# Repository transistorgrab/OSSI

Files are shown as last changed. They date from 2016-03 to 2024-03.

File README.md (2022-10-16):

# OSSI
Open Source Solar Inverter - Software, Hardware, Mechanics

This repository initially clones all content from the former Sourceforge hosted project site (https://sourceforge.net/projects/os-si/). Since the outages on Sourceforge became more frequent, I decided to change over to Github which seems more reliable at this time.

This project aims to build an Open Source (Software and Hardware) Solar Inverter.

The goal is to design a solar inverter with parts that are available trough common distributors with no special manufactured parts.

All documentation (software, hardware, mechanics) is open and free to use by everyone.

Solar inverters can be very complex devices to build and there is a lot to learn on the way.

Join, collaborate, learn and help make the world a better place.

The sun shines for everyone! 😊

The current activities take place in the [Wiki](https://github.com/transistorgrab/OSSI/wiki), where we collect the requirements.

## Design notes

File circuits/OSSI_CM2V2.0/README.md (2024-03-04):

# O.S.S.I Control Module 2 V2.0

This version of the control module contains various improvements over version 1.0/1.1 of the module.

## Breaking Changes
### Different controller pin mapping.
This change was necessary due to an oversight when assigning pins to PWMs. Now the bridge controlling PWMs are assigned to timer 1 channel 1 and 1N and channels 2 and 2N which now implements requirement SOFT-3002.

However, the module footprint still shows the same pin mapping as before.

## Improvements
The board now features an I²C EEPROM for storage of parameters, settings, counters and other data that should be protected between firmware updates. This is an actual EEPROM and not a Flash due to vastly better data retention and write cycles.

The package of the 8 pin ICs on the module are now changed to TSSOP to improve use of board space.

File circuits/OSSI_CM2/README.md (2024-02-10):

This is the Control Module 2.

It's based on a STM32L412 ARM M4 microcontroller.

It's designed for 3.3 V input voltage.

It features a 2.5 V and 1.25 V reference voltage source and a digital temperature measurement IC.

On it's pins provides:
* 3.3 V filtered analog voltage
* 2.5 V reference voltage, 1.5% accuracy
* 1.25 V reference voltage, 1.5% accuracy
* 8 analog inputs
* 11 digital outputs
* 1× UART (RX/TX)
* 1× I²C (Clk/Dat)

[O.S.S.I. CM2 pinout](./bom/OSSI_CM2-Pinout.pdf "Pinout of the O.S.S.I. Control Module 2")

## Remarks
When building the board by hand the voltage devider R132/R133 can be realized by using 1% resistors. However, one needs to value-match them to be within the 0.1% tolerance.

For example: When using 1 kΩ resistors they need to be within 1 Ω difference to each other.

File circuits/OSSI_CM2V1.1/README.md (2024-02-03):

# O.S.S.I Control Module 2 V1.1

This version of the control module contains only bug fixes to version V1.0.

These are either changes to the BOM (values of components) or changes on the PCB which are only fixable on version 1.0 by hardware modifications.
Changes to the PCB are limited to fixes that restore the original design idea. E.g. connection of a voltage divider to the correct net to remove undesired voltage drop.
Component references and positions are kept the same as on version 1.0.

If there are hardware modifications that add components, add functionality or remove functionality these must be done in a version 2.0 of the module.

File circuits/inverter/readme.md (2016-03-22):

This directory contains all schematics for the inverter.
It is planned to place all components on a single board (electronics and power electronics) since this is the best way to keep the costs down and keep the system complexity low.
Mulitple boards require connectors and cables. Connectors can go bad over time (corroding contacts due to moisture), cables add their own problems due to EMI and ground bounce. The connection between cable and connector is an additional source for failure.

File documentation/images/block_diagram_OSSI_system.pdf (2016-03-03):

Author: | os-si-man | Date: | 2015-03-22

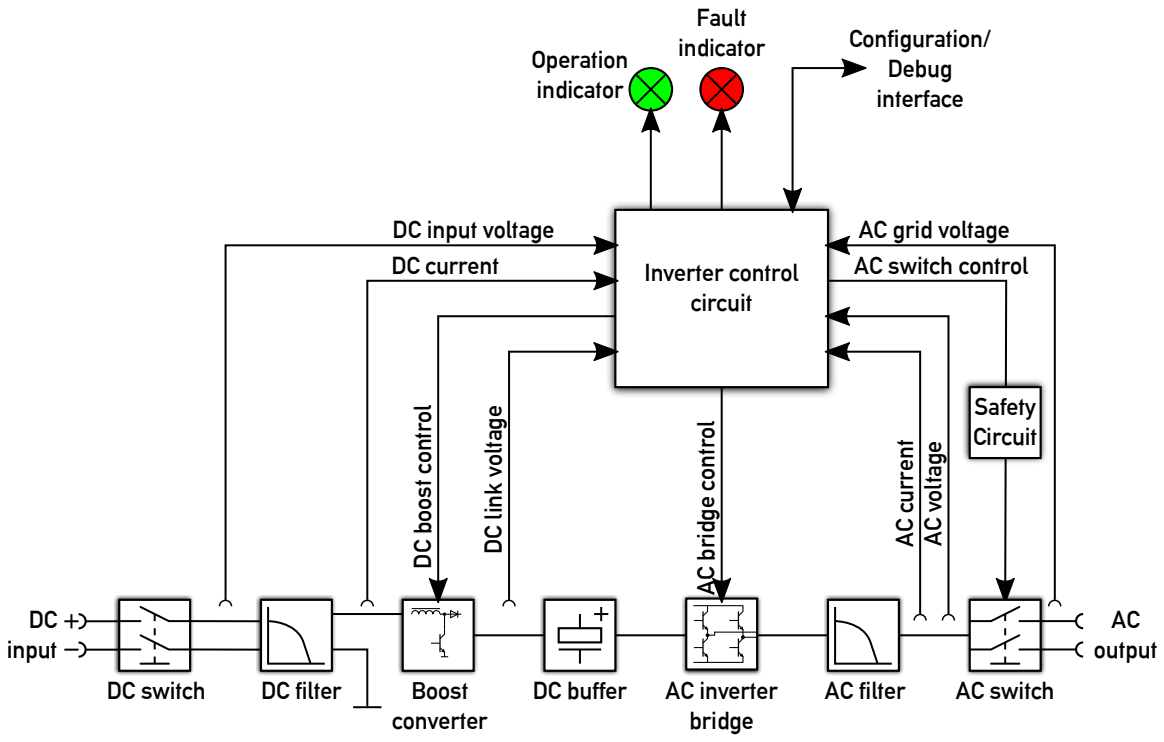
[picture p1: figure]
DC input; DC switch; DC filter; Boost; converter; AC output; AC switch; DC boost control; AC bridge control; AC current; AC voltage; AC switch control; Operation indicator; Configuration/ Debug interface; Fault indicator; DC input voltage DC currentDC link voltage; Inverter control circuit; AC grid voltage; Safety Circuit; AC inverter; AC filter; bridge; DC buffer

Project: | Open Source Solar Inverter (OSSI)

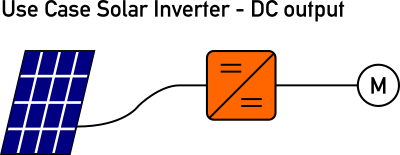
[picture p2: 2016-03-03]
documentation/images/OSSI_use_case_solar_dc.png

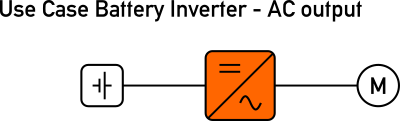
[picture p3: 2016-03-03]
documentation/images/OSSI_use_case_battery_ac.png

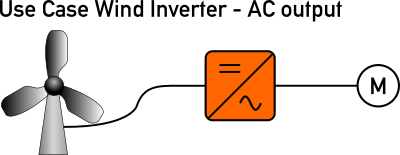
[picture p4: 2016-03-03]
documentation/images/OSSI_use_case_wind_ac.png

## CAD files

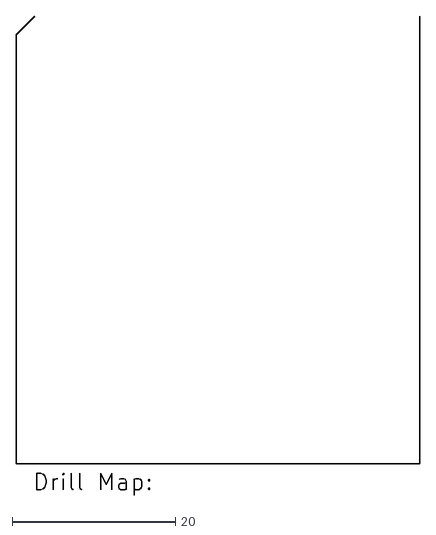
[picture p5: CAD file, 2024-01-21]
circuits/OSSI_CM1/fabrication/OSSI_CM1-NPTH-drl_map.dxf
49.5 x 58.7

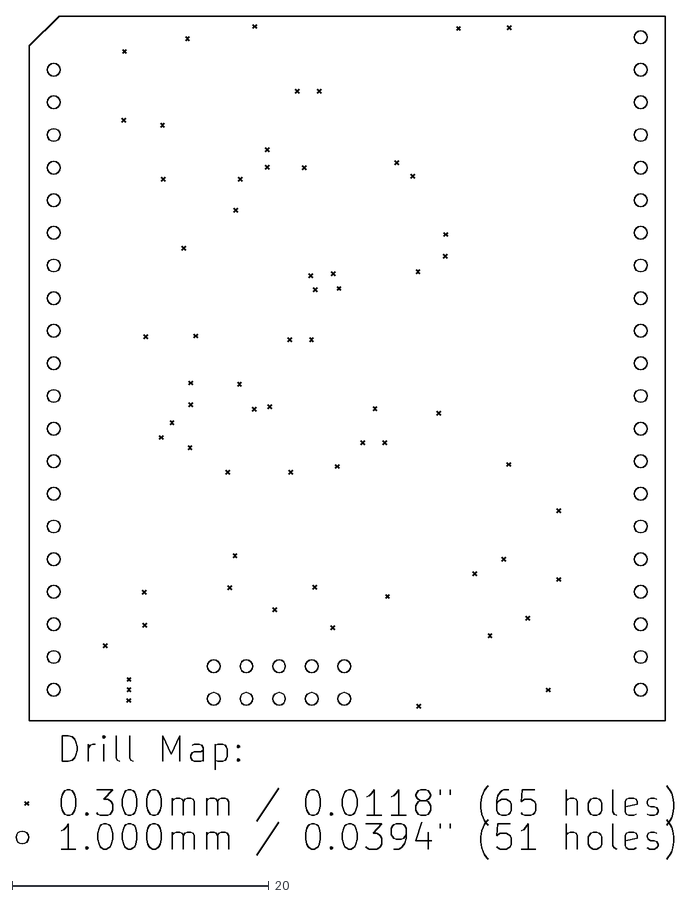
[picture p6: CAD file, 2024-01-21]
circuits/OSSI_CM1/fabrication/OSSI_CM1-PTH-drl_map.dxf
51.2 x 65.6

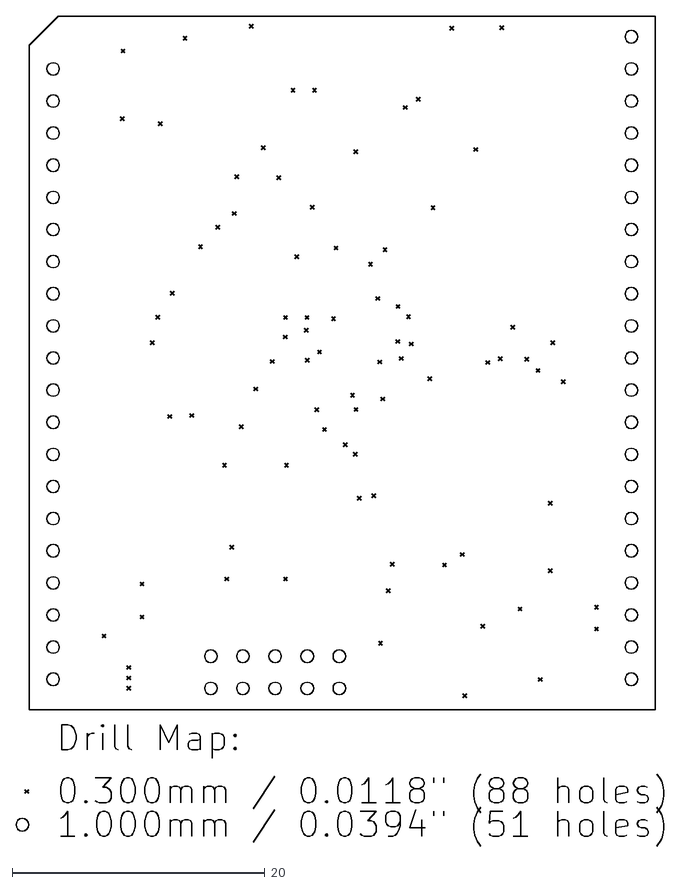
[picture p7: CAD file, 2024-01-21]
circuits/OSSI_CM2/fabrication/OSSI_CM2-PTH-drl_map.dxf
51.2 x 65.6

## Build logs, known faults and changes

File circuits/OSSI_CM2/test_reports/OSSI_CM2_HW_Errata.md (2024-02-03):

# Errata for Board Revision V1.0 of Control Module 2

## Error
The voltage divider for reference voltage ```1V25_REF``` is connected on the wrong signal (```2V50_REF```). This leads to a too low reference voltage output on the signal ```1V25_REF```. 

## Solution
The voltage divider ```R133```–```R132``` needs to be connected directly to ```pin 7``` of ```U104```.
To achieve this one needs to cut the signal trace for ```2V50_REF``` between ```R134``` and ```R133``` and the trace between  ```R133``` and ```pin 3``` on connector ```X201```.
Then solder a wire from ```R134``` to ```pin 3``` on connector ```X201``` and a wire from the signal connecting ```pin 7``` of ```U104``` and ```R134``` to the now unconnected pad of ```R133```.

This error is **solved on Board Revision V1.1**.

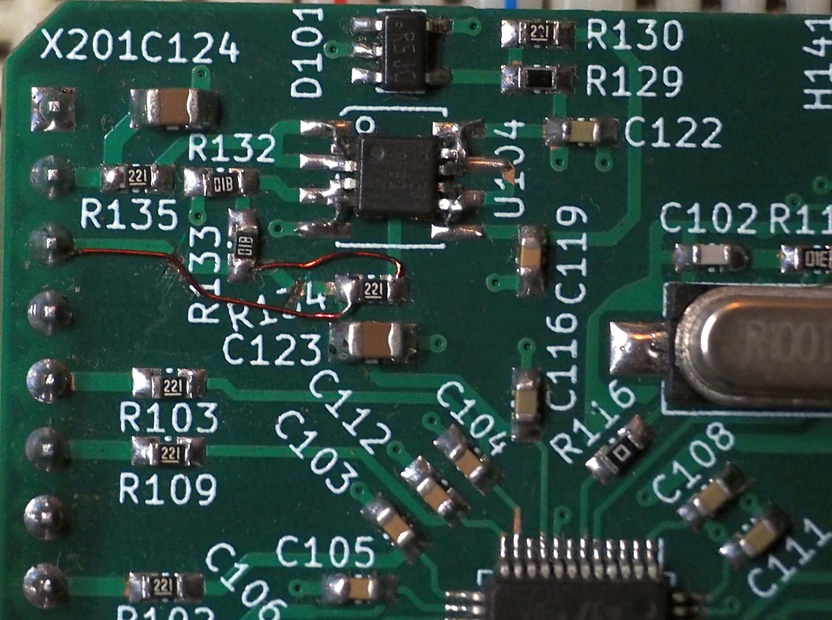
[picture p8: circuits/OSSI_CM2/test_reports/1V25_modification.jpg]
1V25 modification 1V25_REF modification on CM2 V1.0


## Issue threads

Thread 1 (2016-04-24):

Need anything?

tyrel, 2016-04-24:
Hi! I ran across your project because I was looking to see if there was anyone working on an open-source solar inverter, in order to get around problems I and my friends have experienced with trying to get data from our proprietary inverters. So I'm excited to see that you're working on this. I would love to help.

I have some limited knowledge of electronics (e.g. I know what a resister does and why they are used, but don't know how to figure out which one to use), enough to put together a weather station from scratch. I know how electricity works at the atomic level. But I'm primarily a software guy, and have done projects on Raspberry Pi and Arduino, and other low-level stuff like operating systems development. I'm currently working on a remote solar-powered weather station using a Raspberry Pi with ZigBee communications.

As far as solar: I have a 12 kW solar array, my wife works at a solar installer, and I know people at a local solar module manufacturer. I know how it works, I know what MPPT is, etc.

I've looked a bit at your wiki but have more to go through. Is there somewhere, based on my skills, you can recommend that I start looking at? Any questions I can help find answers to?

Thanks!

transistorgrab, 2016-04-24:
Hi Tyrel,

Thanks for your message.
I'm currently stuck at the power electronics stuff like which inductor to choose our how to realize the power inverter circuit since my background is the electronics and analog part.
However, I also would love to get support on the software side of things.
I'm proposing using a RTOS as a base like FreeRTOS (http://www.freertos.org).
But this needs to be ported and set up for the chosen controller. Also a basic structure for the scheduling of all the required tasks needs to be defined and so on. The software/firmware is a project of itself… ;)
So whatever you want to do on this side of the project (and planning) is greatly appreciated.
I keep all the documentation in the Wiki because I find it the easiest way with no tool required.

Best regards,
  André

stardust85, 2021-11-21:
Hi, I can offer my limited very knowledge of hw programming (from high and a bit from university) and tons of experience of sw development experience...

I am also a proud owner of a 4.56 kWp hybrid roof-top sytem based on the RCT inverter, BMS and batteries.

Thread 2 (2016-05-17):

Expansion to battery use

sheppy99, 2016-05-17:
Is it worth expanding your project at some stage to include use with batteries? I'm thinking some sort of monitored situation whereby assuming the battery has sufficient charge, and assuming there is import electricity, that the inverter supplies just enough output if headroom is available to reduce the import to  a few watts. It could use a feed from Open Energy Monitor or similar to provide the instantaneous import / export power information.
In many parts of the world exported energy is something to be avoided, and importing is expensive

transistorgrab, 2016-05-18:
Yes. There is no principal obstacle to use batteries as an input source.
It's one of the use cases. You only need to adjust the input voltage range to not drain the battery too low and also you have to disable the "Maximum Power Point" algorithm. This is "only" a software issue. Nothing that the hardware does not support.
For communication a UART (serial) port is provided in the design, usable for debug or other uses.

sheppy99, 2016-05-18:
Thanks for the reply, will it be possible to vary the output of the inverter so generated power matches used power? I guess several could be built as a lower power design and switched as needed but that seems a little inelegant

transistorgrab, 2016-05-20:
The first can also be achieved via communication and setting a current limit. But this would require an external device that monitors energy flow from and to the grid. I think most of the energy flow control intelligence then needs to be placed in that device, since I fear that would exceed the computing power of the main controller.
The second could be achieved in the software that keeps track of the state of charge of the battery. but it depends on what kind of Lithium battery is in use. You need definitely a battery pack with a battery management system (BMS). (The inverter can not track all cells of a battery pack.)
The BMS (at least those I know) keep track of the state of charge of the battery. It remains to implement a communication interface to the battery/BMS. Some use CAN, I think there are also some that use other serial interfaces.
My opinion is, that lithium batteries are quite complicated in handling and operation. Therefore at least in the first iteration of the inverter only lead batteries can be used (no additional communication required, only cut off voltage must be respected).

sheppy99, 2016-05-22:
I wonder if the inverter could take something like a MQTT message to tell it how much power to output? That could be generated by an energy monitoring system such as Open Energy Monitor, with an automation system such as Openhab stacked on top. If the inverter sent out its status, decisions could be made on both power demand and charge remaining and the requested power output could be modified in light of reported input voltage.
The automation system can take control of what the inverter is asked to do, with the inverter maybe going into a failsafe mode if it hasn't received a valid message for a period of time.
Obviously a BMS is very important for both safety and longevity!

transistorgrab, 2016-06-08:
Seems possible, just depends on how much overhead the communication protocol generates. It may be necessary to have a gateway that translates "inverter protocol" to "(home) automation protocol".
On the other hand if there is a light weight protocol freely available that could be implemented as the standare protocol for the inverter communication.
For example Modbus could be used ([freemodbus.org](http://www.freemodbus.org/)) but I don't know about the specifics.

Closed 2019-08-01.

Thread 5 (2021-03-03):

i would like to help

Thorbijoern, 2021-03-03:
Hi,

i'm researching inverter design for some time now, because i noticed a lack of open source inverter projects. There are open source MPPT charge controllers and BMS, but no inverters. I only recently found this project but think your work is great!
I have documented a lot of stuff i found about inverters here: https://thorbijoern.github.io/wiki/#inverter%20(Wechselrichter) maybe it is helpful to you (i need to do some ordering though).
I would like to contribute to this project, because the goal of my researching was to create my own design, but i still have a lot to learn.

i've only read a small part of the documentation as of yet, but in #1 you said you would need help on the software side (even though it's from 2016). I'm a software developer by profession and could help you with that part.
I also could improve the documentation a bit.
My electronics knowledge is limited and i haven't done anything powerelectronics myself yet, but i think i have a good overview.

this project also intersects with the projects from https://libre.solar/ and https://www.ose-germany.de/ (https://wiki.opensourceecology.de/Open_Source_Ecology_Germany) and others and compatibiltity/interoperability between the designs would be great.

Tank you for the great work so far!

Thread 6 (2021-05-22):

Project status

pixelpoppul, 2021-05-22:
Is this project still continued or forgotten?

transistorgrab, 2021-05-25:
Hi, it's not forgotten but dormant.

I have other things currently taking up my time. But if you're interested in helping I would gladly support and wake it up again and switch my priorities. :) It's a bit boring to do all the things alone…

pixelpoppul, 2021-05-25:
Would be great to continue given there arent much open source systems on the internet and the solar market is kinda booming :) mention when you left off and we can continue it

transistorgrab, 2021-05-25:
Take a look at the latest Kicad files (just uploaded my latest modifications). I think I have a lot of the electronics in a good state. However, power electronics like AC inverter bridge and drivers are still open. This is the part where I have not the deepest knowledge and need to learn most. Which is why it's the last to be finished.

Software is totally open. I figured it's not much use to start anything software as long as it's not defined what hardware will be there and what needs to be considered in software.

Also look into the wiki section here. I documented as much as possible there. Read it over and see if it helps to understand what I wanted to create here. I'm open to feedback so don't hold back.

pixelpoppul, 2021-05-25:
Its not THAT complicated as three basic things
Sensing
Driving the hbridge
Output control

I have rough schematics to do all three along with the hbridge  ill look at the kicads once i get time   like 20mins from now

pixelpoppul, 2021-05-26:
do you have a email i could send you a sample file to? it has almost all of the things required(almost) all already kinda made

transistorgrab, 2021-05-26:
you can send me your file to ansc _dot_ de _at_ gmail _dot_ com

looking forward to it :)

pixelpoppul, 2021-05-29:
I think i missed the page we were on  the file i sent was for a microinverter as this project looks like a string inverter.  I think it will be easier on you to build a microinverter as its easy to code and design and is also cost efficient  :)

Thorbijoern, 2021-06-01:
i'm happy to see that there is some new developments here, after i didn't receive an answer on #5 i worried this is dead.

i think the types of inverters (string, micro, etc.) are a bit confusing.
Judging from OSSI-2002 from [Requirements Page](https://github.com/transistorgrab/OSSI/wiki/The-Requirements) it seems like a micro inverter ist the goal, but it should also have a very high input voltage like string inverters OSSI-2003.
I  don't know how one can accieve input ranges from ~18V for single solar panels and ~12V or ~24V for batteries, up to 600V. But i also don't know how one designs such boost stages and https://github.com/transistorgrab/OSSI/wiki/Electronics-and-Electrical#power-supply also talks about problems with the input range and efficiency.

libre.solar is also cool, they have some open MPPT charge controller designs and they make documentation on the design princibles, controlling and other things which might be helpful here too.

pixelpoppul, 2021-06-01:
There are solar panels tjat output 24v and custom ones do as much as 50!.
Boost stages are nothing but just the transformer stepping the sine wave made by the full h bridge system. Bssic but works
SPWM gives a higher return range and increases efficiency but it is hsrd to code on a microcontroller as the timings need to ne near perfect for a grid level pure sine wave inverter.

transistorgrab, 2021-06-02:
@Thorbijoern Sorry for missing your message on #5. With the current situation it's a bit stressful to keep everything monitored.

There are different design goals here because I want to be able to realize different devices with as few as possible changes to the overall design. It's not aimed towards making the cheapest inverter on the planet but as a learning experience. I hope to make a as good as possible documentation about all design decisions for others to see what it takes to make a working inverter.

String inverters have multiple panels in series. Microinverters connect to one or two panels in parallel.
I think it is possible to have a small solution that only takes one panel and charges a 12 V battery. But also a solution that takes a panel string and charges a higher voltage battery.
Or it runs off a battery instead of a solar panel.

It's great that there are so many different projects now. :)

Just take a look at what is already there and ask questions or propose some measures or changes. I still have hopes that some day there will be a prototype. :D

casainho, 2022-02-16:
Hi.
I would be interest in having a Telegram channel so the development could be discussed. I am on 2 channels doing real development for EBike and EScooter motor controllers, all OpenSource projects.

@transistorgrab would you like to created a Telegram channel for developers on this project?

Congratulations on this project, Solar and Battery seems will be a BIG thing in next years!!

transistorgrab, 2022-10-03:
Hi @Saphira8105,
This project is dormant at the moment. Due to real life happening I did not find much time for it.
However, if someone joins I would gladly revive it.
Main problem at the moment is the power electronics stuff. I'm not an expert at this and this is a blocker for the actual important part of "inverter".
Some side-projects showed me that one may think it's OK but when actually operating the thing it can show unexpected behaviour and break if you do not know exacly what you are doing.

transistorgrab, 2022-10-05:
This project is still open for development. However, I'm stuck at the power electronics part, where the actual "inverter" function is affected. I'm no expert on this and had some experiments done that showed if you don't know what you're doing it will not work (reliably). So if you know someone who has some experience with power electronics, that could give the project new life.

pixelpoppul, 2022-10-05:
I'll surely take a look at it but can you brief what's not working reliably? Is the bridge not timed right or what is it?On Oct 5, 2022 9:37 PM, "André S." ***@***.***> wrote:
This project is still open for development. However, I'm stuck at the power electronics part, where the actual "inverter" function is affected. I'm no expert on this and had some experiments done that showed if you don't know what you're doing it will not work (reliably). So if you know someone who has some experience with power electronics, that could give the project new life.

—Reply to this email directly, view it on GitHub, or unsubscribe.You are receiving this because you authored the thread.Message ID: ***@***.***>

transistorgrab, 2022-10-05:
Currently there is still no actual hardware. The schematics shows the latest version.
To summarize: on the DC input there still needs to be decided what is the right IGBT for the boost converter. There is only a generic part in the schematics.
The inverter bridge is completely blank. There is input required what are the right components for the desired power class.
For the Bridge drivers there is a first suggestion but the circuit is not designed. But this is just a minor issue.

Adding to that the component selection needs to be documented in a way that makes it clear without doubt why a certain component or ciruit was chosen to make it easier for later contributors if a change is required.
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
pixelpoppul, 2022-10-05:
Looks like we have a solid plan, let's just hope we don't get the magic smoke XD. 600w is doable and the spwm may need some tuning because sine waves made by the inverter will be absolutely distorted due to the loads

HyGy, 2022-10-11:
Is there now a board/parts list to build?

It will be good if this thing is supported by ESPHome, and then we can integrate it for example to homeassistant.

I think what is required:
- battery charging (Settable parameters)
- solar input
- if there is not enough power in the batteries/solar then add suplement from the grid
- serial output/input to control/monitor the device parameters/consumption/voltages

What is a really usable a 5KV system I think. Bot for start about 700VA is good.

What is the state now?

transistorgrab, 2022-10-16:
Hi @HyGy,

There is still no fixed parts list. Some parts of the circuit are still not finally designed yet.
Additional problem that came up in the last few days when I reviewed the design is that the chosen microcontroller is currently not available anywhere.
If anyone has an idea what a good and available second source is, I'm open for suggestions.
I found some AVR32 based parts, PIC32 based parts even a Renesas part on digikey but I cannot say how feasable they are for this application.

Regarding ESPHome I don't think this should be intergrated into the controller software. I'm more thinking about an open protocoll where an external interface-converter then implements the required protocoll for home automation. e.g. an ESP32 that talks on one end to the inverter (via wired interface) and provides the desired protocoll via WiFi.
This would also solve the problem of isolation of the communication interface because the ESP32 could be connected to the hot potential of the inverter.

Waynedejager1, 2022-11-08:
I have a vested interest in this space and would like to help where possible. My main area of interest would be in the 100KW range of product and would be wiling to assist with the project. Areas where i can offer assistance :- 1) Current commercial unit damaged samples 2) Development funding once the core dev team is established 3) Procuring samples and testing in real life application.

If this appeals to you Andre @transistorgrab then please keep me informed. Wayne

transistorgrab, 2022-11-09:
Hi @Waynedejager1,

thanks for your offer.

Currently I'm back on square 1 regarding the main controller of the device.

The one I picked when starting the project looked like the perfect candidate.
However, currently it's nowhere available and I'm not a big expert on controllers to know which of the currently available parts would fit the bill. Also prices for components available now seem to be much higher than a few years ago.
So, research on this is slow until I find a part that looks OK or someone comes up with a suggestion. If you know of someone who can suggest a part I gladly look into it. 😄

vkylamba, 2023-05-03:
@transistorgrab Is it still active? I would be interested to contribute.

transistorgrab, 2023-05-04:
Hi @vkylamba,

this project is not abandoned, thanks for your interest. :)

Current status is, that I need to find a replacement for the currently planned controller of the inverter (it's not available right now).
Since I'm not familiar with many controllers I'm open for suggestions.
Currently I think about changing the design so that the controller sits on a separate board so that it's easier to only change the controller depending on availability and not to have to change the whole board.

vkylamba, 2023-05-07:
@transistorgrab thank you for the response. Maybe one of the [STM32F0x0](https://www.st.com/en/microcontrollers-microprocessors/stm32f0x0-value-line.html) series microcontroller can be used, e.g. [stm32f030cc](https://www.st.com/en/microcontrollers-microprocessors/stm32f030cc.html). If you can list the features, I can look up the available controllers.

sslupsky, 2025-02-17:
It occurs to me a good use case for this would be off grid cabins and RV's for users that boon dock.   Existing inverter/chargers are bulky and heavy.  Something more modern designed with GaN power stages would improve efficiency and reduce weight and size considerably.  Target AC power output for this would be about 3500 watts but 2500 watts would be adequate for a lot of users in this space as well.  Should be able to operate from 12V/24V/48V lithium batteries and 200W/400W of solar panels.  Ability to plug into the mains supply to quickly charge the battery and/or provide bypass.

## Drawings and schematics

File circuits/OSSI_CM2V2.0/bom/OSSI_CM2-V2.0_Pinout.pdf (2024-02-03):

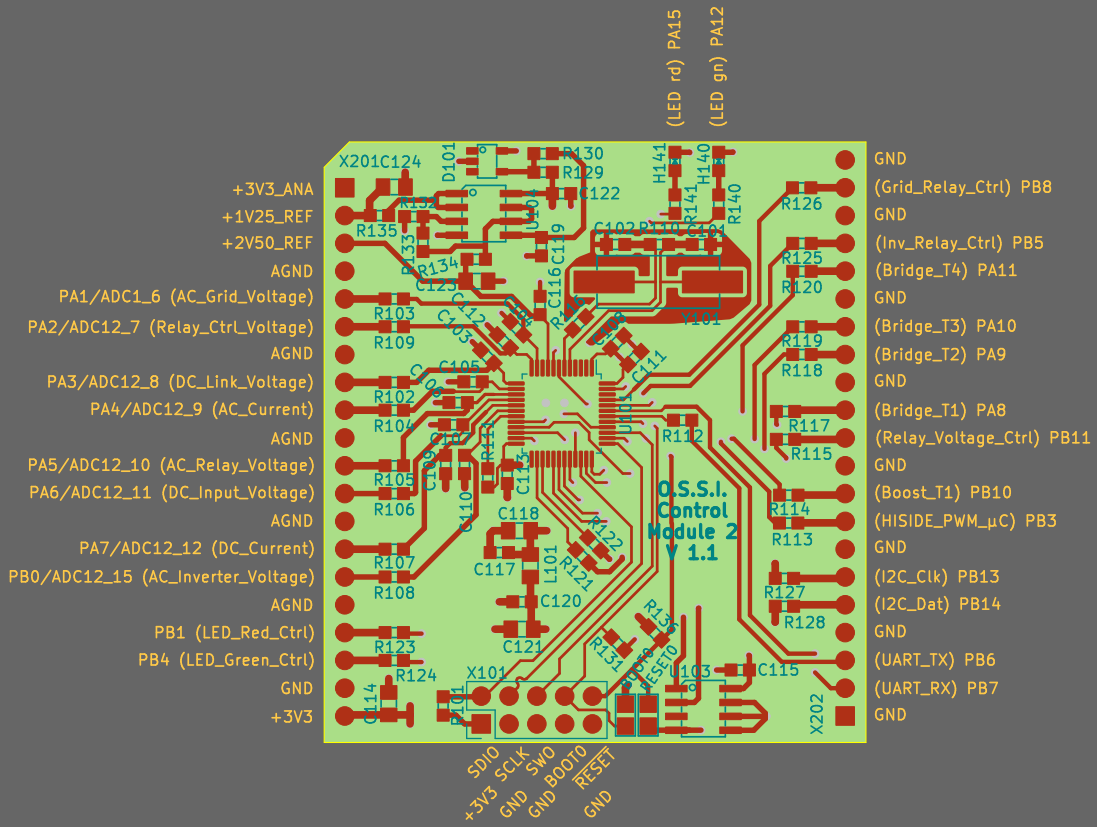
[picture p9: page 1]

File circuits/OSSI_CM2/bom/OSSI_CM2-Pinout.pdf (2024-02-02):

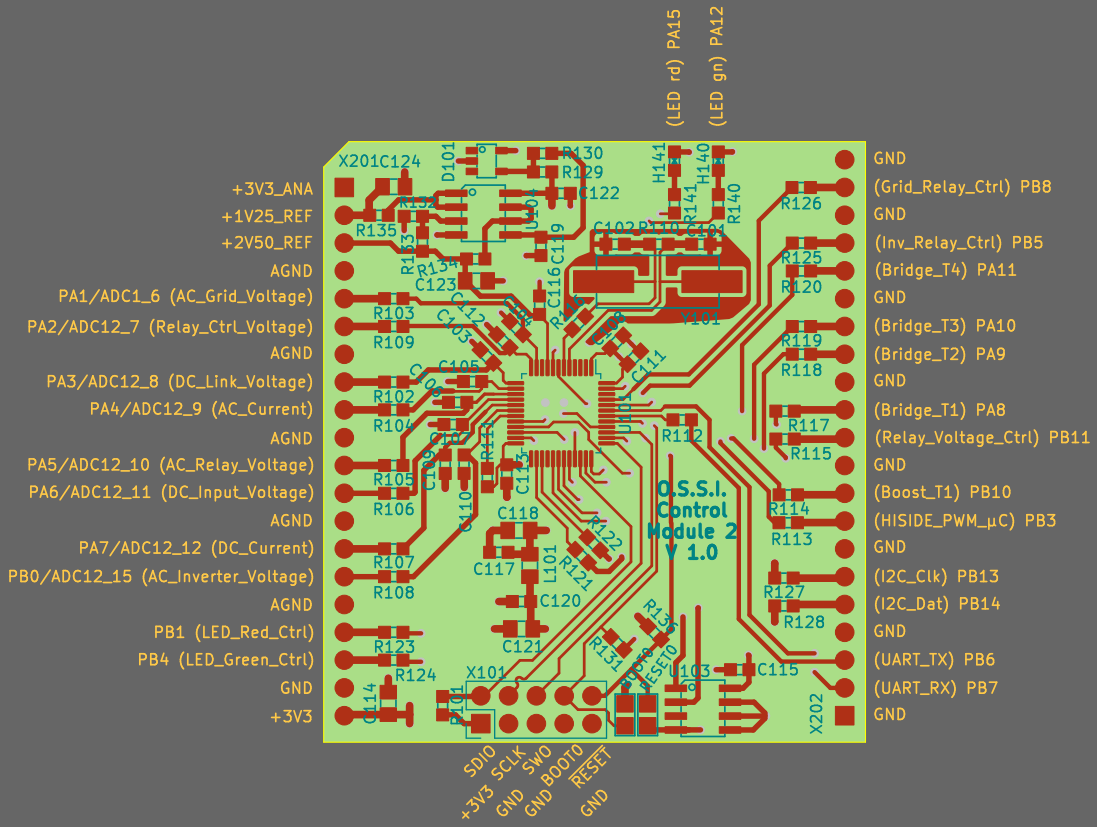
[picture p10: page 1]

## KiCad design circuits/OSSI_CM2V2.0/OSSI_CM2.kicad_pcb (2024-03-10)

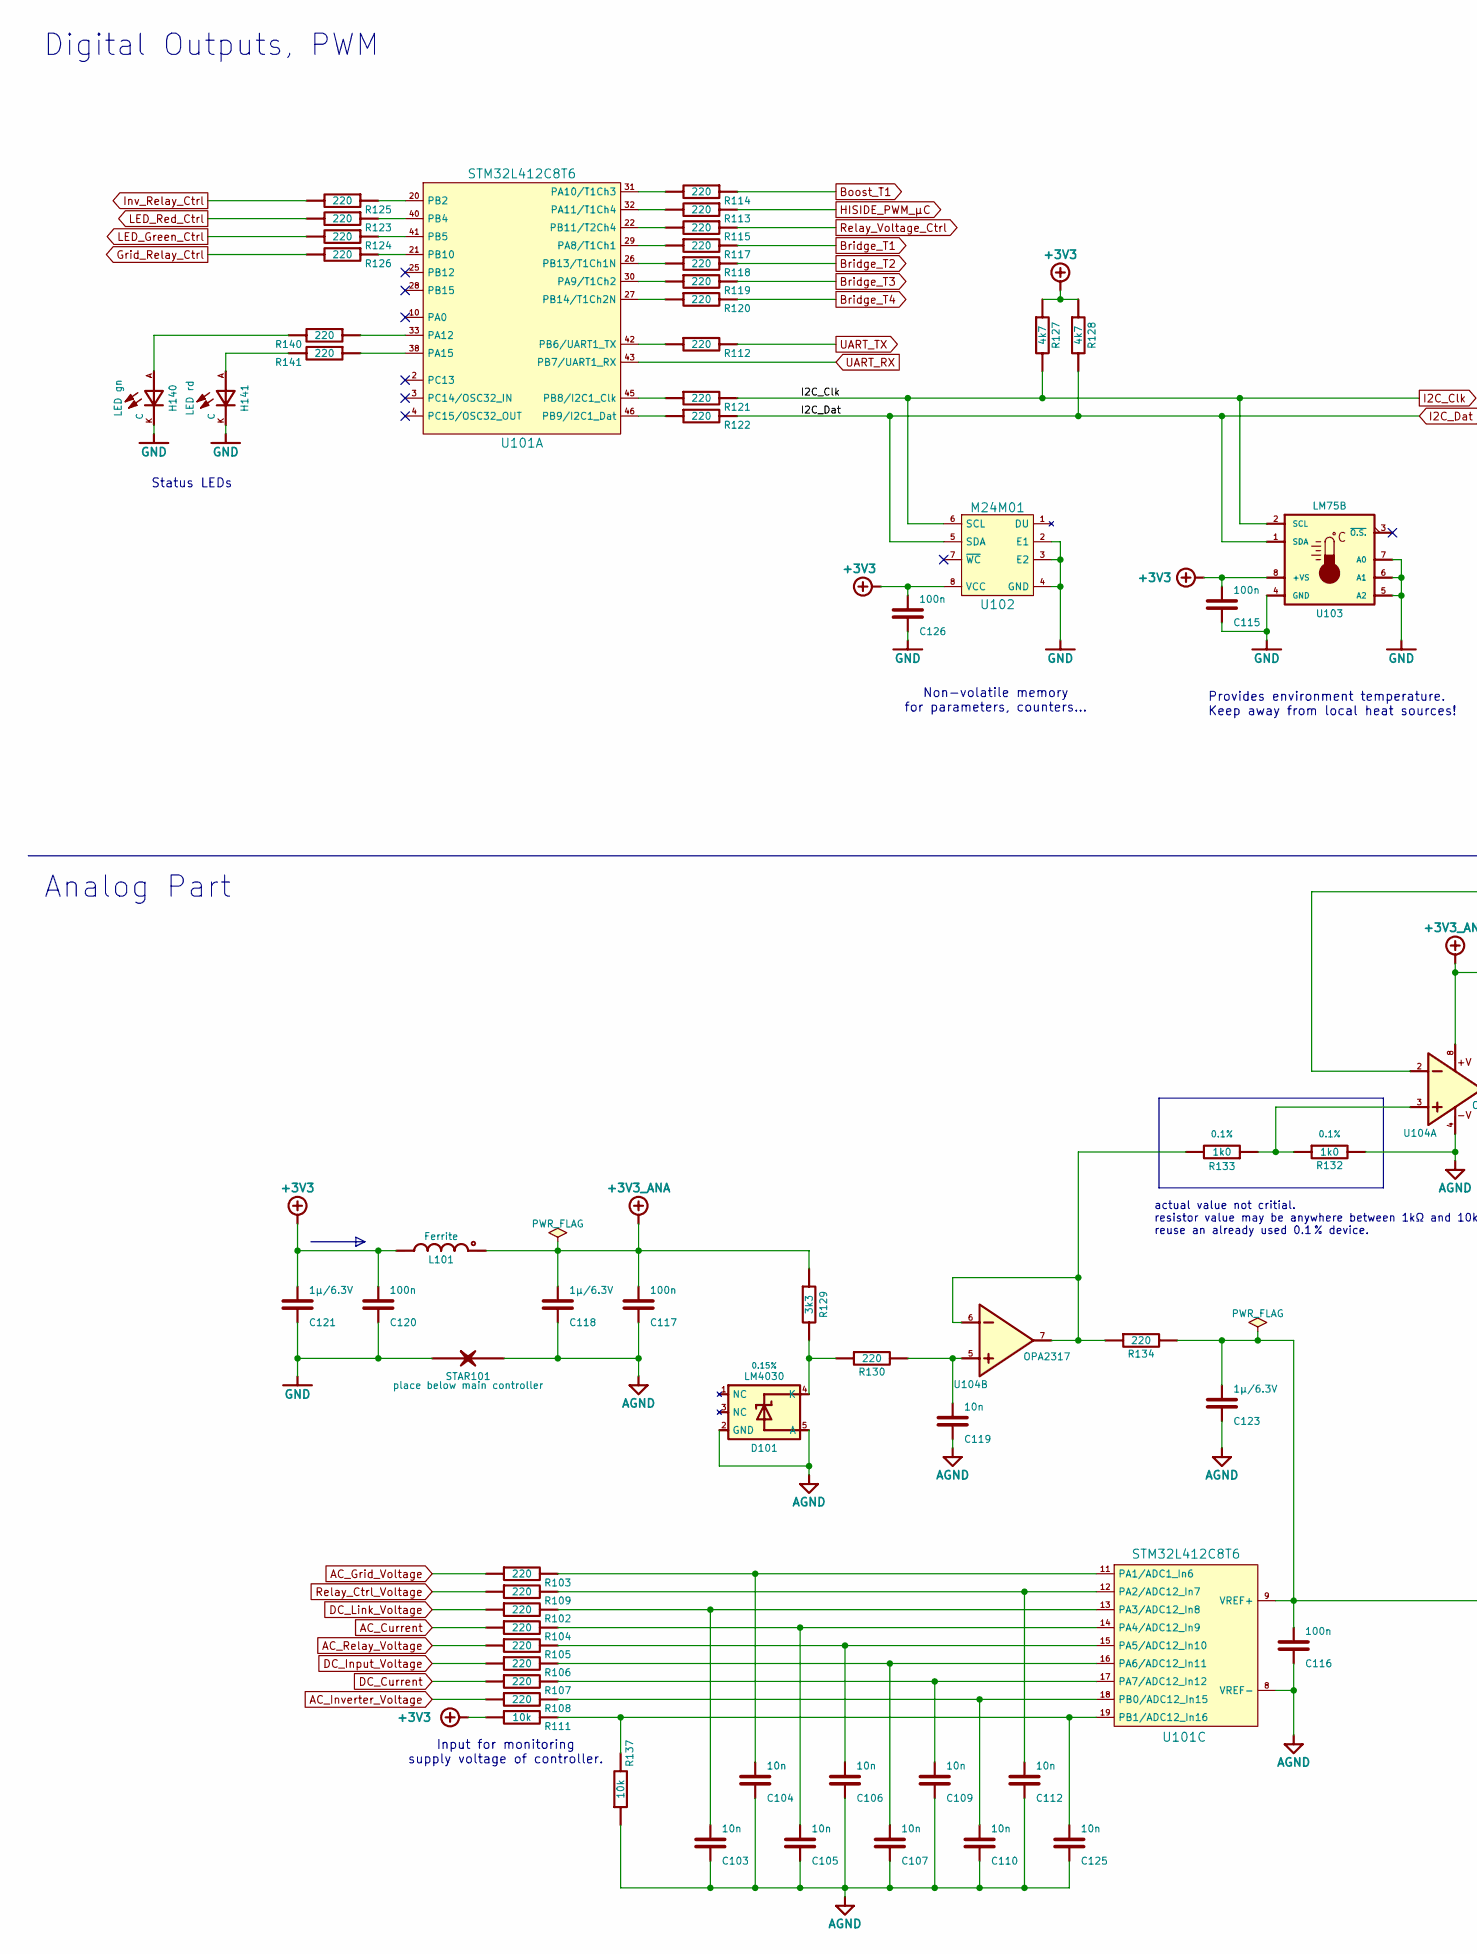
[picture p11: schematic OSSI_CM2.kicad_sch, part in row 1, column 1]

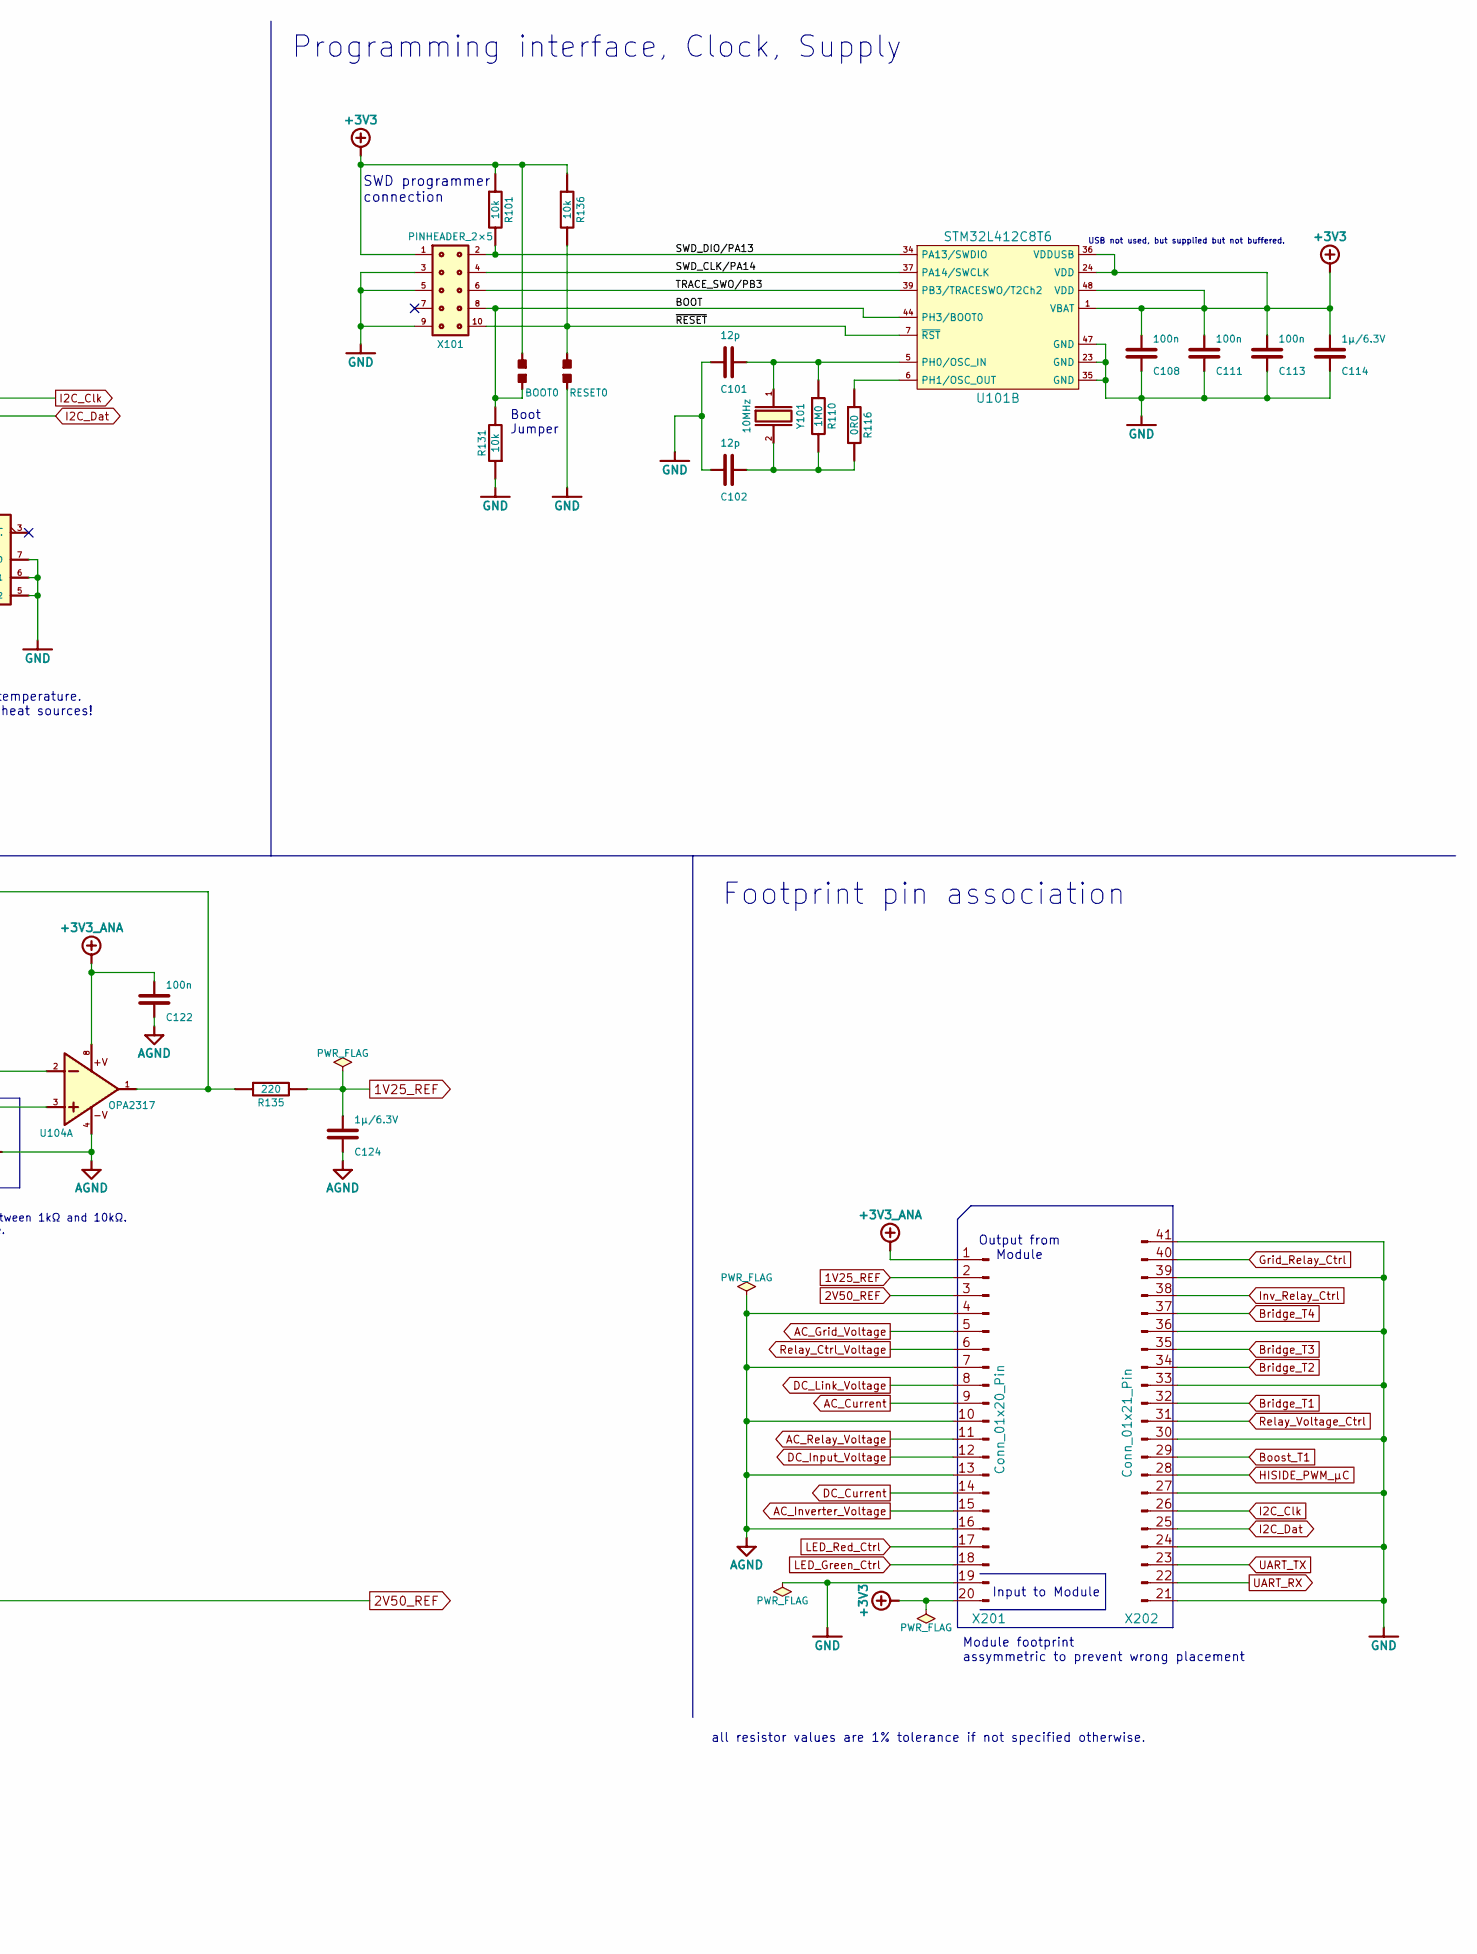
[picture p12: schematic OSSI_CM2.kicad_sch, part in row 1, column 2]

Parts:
BOOT0: Solder_bridge_open; JUMPER_OPEN
C101, C102: 12p; 0603_W_C; Tolerance %; Partnumber P
C103, C104, C105, C106, C107, C109, C110, C112, C119, C125: 10n; 0603_W_C; Tolerance %; Partnumber P
C108, C111, C113, C115, C116, C117, C120, C122, C126: 100n; 0603_W_C; Tolerance %; Partnumber P
C114, C118, C121, C123, C124: 1µ/6.3V; 0805_W_C; Tolerance %; Partnumber P
D101: LM4030; SOT-23-5; Tolerance 0.15%; Partnumber P
H140: LED gn; 0603_W_LED; Partnumber P
H141: LED rd; 0603_W_LED; Partnumber P
L101: Ferrite; 0805_W_L; Partnumber P
R101, R111, R131, R136, R137: 10k; 0603_W_R; Tolerance %; Partnumber P
R102, R103, R104, R105, R106, R107, R108, R109, R112, R113, R114, R115, R117, R118, R119, R120, R121, R122, R123, R124, R125, R126, R130, R134, R135, R140, R141: 220; 0603_W_R; Tolerance %; Partnumber P
R110: 1M0; 0603_W_R; Tolerance %; Partnumber P
R116: 0R0; 0603_W_R; Tolerance %; Partnumber P
R127, R128: 4k7; 0603_W_R; Tolerance %; Partnumber P
R129: 3k3; 0603_W_R; Tolerance %; Partnumber P
R132, R133: 1k0; 0603_W_R; Tolerance 0.1%; Partnumber P
RESET0: Solder_bridge_open; JUMPER_OPEN
STAR101: STARPOINT
U101: STM32L412C8T6; LQFP-48_7x7mm_P0.5mm
U102: M24M01; TSSOP8
U103: LM75B; TSSOP8
U104: OPA2317; TSSOP8; Partnumber P
X101: PINHEADER_2×5; PinHeader_2x05_P2.54mm_Vertical; Partnumber P
X201: Conn_01x20_Pin; PinHeader_1x20_P2.54mm_Vertical
X202: Conn_01x21_Pin; PinHeader_1x21_P2.54mm_Vertical
Y101: 10MHz; HC49_US; Partnumber P

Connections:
1V25_REF: C124.2, R135.2, X201.2
2V50_REF: C116.2, C123.2, R134.2, U101.9 (VREF+), X201.3
+3V3: BOOT0.1, C108.2, C111.2, C113.2, C114.2, C115.2, C120.2, C121.2, C126.2, L101.2, R101.1, R111.1, R127.1, R128.1, R136.1, U101.1 (VBAT), U101.24 (VDD), U101.36 (VDDUSB), U101.48 (VDD), U102.8 (VCC), U103.8 (+VS), X101.1, X201.20
+3V3_ANA: C117.2, C118.2, C122.2, L101.1, R129.1, U104.8, X201.1
/BOOT: BOOT0.2, R131.2, U101.44 (PH3/BOOT0), X101.8
/SWD_CLK/PA14: U101.37 (PA14/SWCLK), X101.4
/SWD_DIO/PA13: R101.2, U101.34 (PA13/SWDIO), X101.2
/TRACE_SWO/PB3: U101.39 (PB3/TRACESWO/T2Ch2), X101.6
/~RESET: R136.2, RESET0.2, U101.7 (~RST), X101.10
AC_Current: R104.1, X201.9
AC_Grid_Voltage: R103.1, X201.5
AC_Inverter_Voltage: R108.1, X201.15
AC_Relay_Voltage: R105.1, X201.11
AGND: C103.1, C104.1, C105.1, C106.1, C107.1, C109.1, C110.1, C112.1, C116.1, C117.1, C118.1, C119.1, C122.1, C123.1, C124.1, C125.1, D101.2 (GND), D101.5 (A), R132.2, R137.1, STAR101.1, U101.8 (VREF-), U104.4, X201.4, X201.7, X201.10, X201.13, X201.16
Boost_T1: R114.1, X202.29
Bridge_T1: R117.2, X202.32
Bridge_T2: R118.2, X202.34
Bridge_T3: R119.2, X202.35
Bridge_T4: R120.2, X202.37
DC_Current: R107.1, X201.14
DC_Input_Voltage: R106.1, X201.12
DC_Link_Voltage: R102.1, X201.8
GND: C101.1, C102.1, C108.1, C111.1, C113.1, C114.1, C115.1, C120.1, C121.1, C126.1, H140.K, H141.K, R131.1, RESET0.1, STAR101.2, U101.23 (GND), U101.35 (GND), U101.47 (GND), U102.2 (E1), U102.3 (E2), U102.4 (GND), U103.4 (GND), U103.5 (A2), U103.6 (A1), U103.7 (A0), X101.3, X101.5, X101.9, X201.19, X202.21, X202.24, X202.27, X202.30, X202.33, X202.36, X202.39, X202.41
Grid_Relay_Ctrl: R126.2, X202.40
HISIDE_PWM_µC: R113.1, X202.28
I2C_Clk: R121.2, R127.2, U102.6 (SCL), U103.2 (SCL), X202.26
I2C_Dat: R122.2, R128.2, U102.5 (SDA), U103.1 (SDA), X202.25
Inv_Relay_Ctrl: R125.2, X202.38
LED_Green_Ctrl: R124.2, X201.18
LED_Red_Ctrl: R123.2, X201.17
unnamed: C102.2, R110.2, R116.2, Y101.2
unnamed: C119.2, R130.2, U104.5
unnamed: D101.4 (K), R129.2, R130.1
unnamed: H140.A, R140.2
unnamed: H141.A, R141.2
unnamed: R132.1, R133.1, U104.3
unnamed: R133.2, R134.1, U104.6, U104.7
unnamed: R135.1, U104.1, U104.2
unnamed: R117.1, U101.29 (PA8/T1Ch1)
unnamed: R119.1, U101.30 (PA9/T1Ch2)
unnamed: R114.2, U101.31 (PA10/T1Ch3)
unnamed: R113.2, U101.32 (PA11/T1Ch4)
unnamed: R140.1, U101.33 (PA12)
unnamed: R141.1, U101.38 (PA15)
unnamed: R125.1, U101.20 (PB2)
unnamed: R123.1, U101.40 (PB4)
unnamed: R124.1, U101.41 (PB5)
unnamed: R112.1, U101.42 (PB6/UART1_TX)
unnamed: R121.1, U101.45 (PB8/I2C1_Clk)
unnamed: R122.1, U101.46 (PB9/I2C1_Dat)
unnamed: R126.1, U101.21 (PB10)
unnamed: R115.2, U101.22 (PB11/T2Ch4)
unnamed: R118.1, U101.26 (PB13/T1Ch1N)
unnamed: R120.1, U101.27 (PB14/T1Ch2N)
unnamed: C101.2, R110.1, U101.5 (PH0/OSC_IN), Y101.1
unnamed: R116.1, U101.6 (PH1/OSC_OUT)
unnamed: C104.2, R103.2, U101.11 (PA1/ADC1_In6)
unnamed: C112.2, R109.2, U101.12 (PA2/ADC12_In7)
unnamed: C103.2, R102.2, U101.13 (PA3/ADC12_In8)
unnamed: C105.2, R104.2, U101.14 (PA4/ADC12_In9)
unnamed: C106.2, R105.2, U101.15 (PA5/ADC12_In10)
unnamed: C107.2, R106.2, U101.16 (PA6/ADC12_In11)
unnamed: C109.2, R107.2, U101.17 (PA7/ADC12_In12)
unnamed: C110.2, R108.2, U101.18 (PB0/ADC12_In15)
unnamed: C125.2, R111.2, R137.2, U101.19 (PB1/ADC12_In16)
Relay_Ctrl_Voltage: R109.1, X201.6
Relay_Voltage_Ctrl: R115.1, X202.31
UART_RX: U101.43 (PB7/UART1_RX), X202.22
UART_TX: R112.2, X202.23

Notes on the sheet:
SWD programmer connection
Provides environment temperature. Keep away from local heat sources!
Analog Part
Output from Module
Footprint pin association
Input for monitoring supply voltage of controller.
Programming interface, Clock, Supply
USB not used, but supplied but not buffered.
Module footprint assymmetric to prevent wrong placement
Input to Module
Digital Outputs, PWM
Status LEDs
Boot Jumper
all resistor values are 1% tolerance if not specified otherwise.
Non-volatile memory for parameters, counters…
actual value not critial. resistor value may be anywhere between 1kΩ and 10kΩ. reuse an already used 0.1 % device.

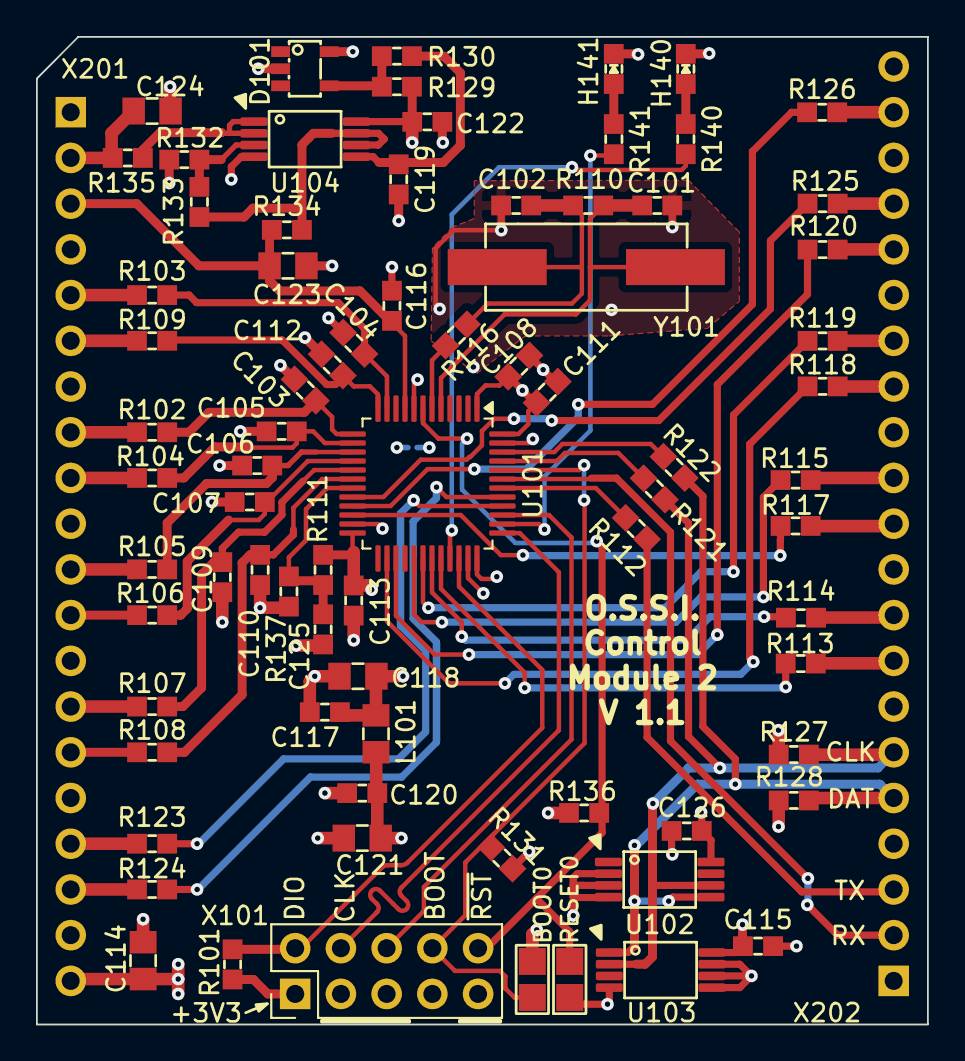
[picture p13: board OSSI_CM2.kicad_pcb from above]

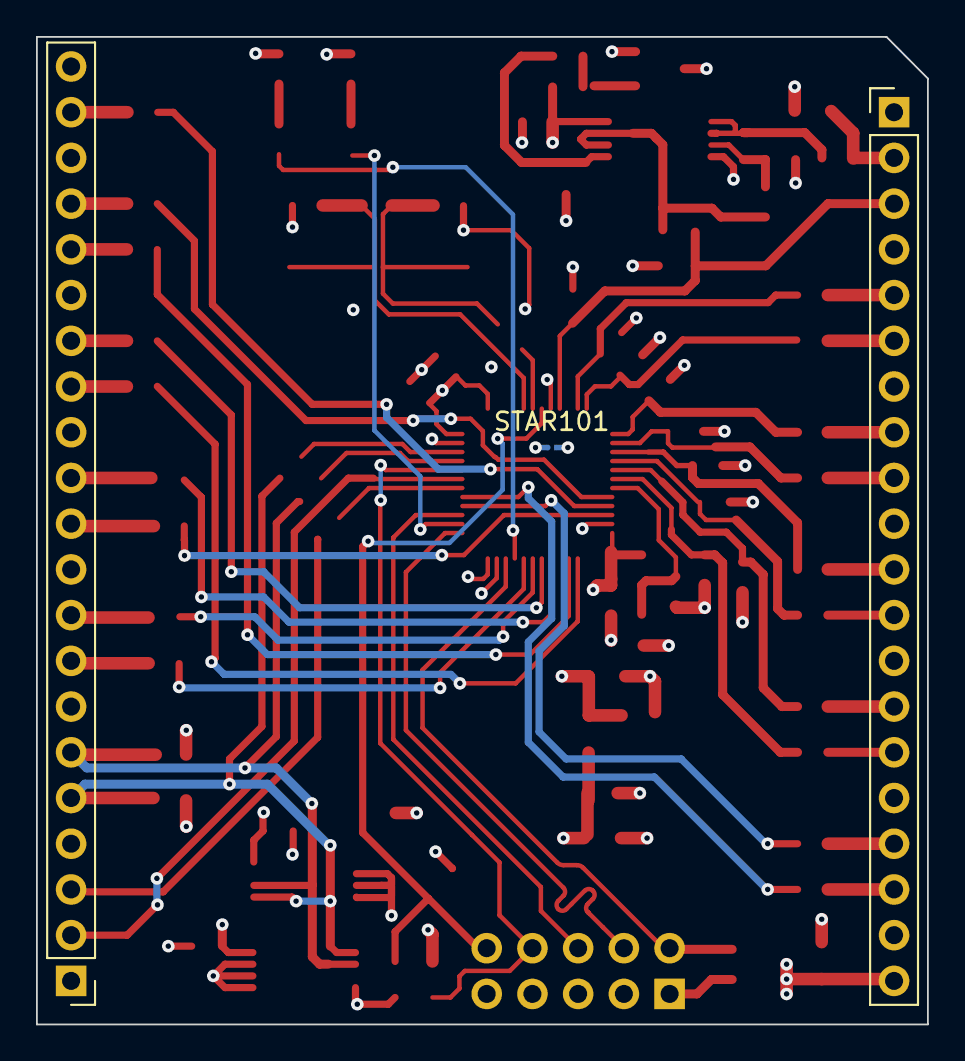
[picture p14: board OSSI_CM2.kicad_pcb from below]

Board: 4 copper layers, 49.5 x 54.9 mm, 80 parts (3 on the bottom side), 69 nets.

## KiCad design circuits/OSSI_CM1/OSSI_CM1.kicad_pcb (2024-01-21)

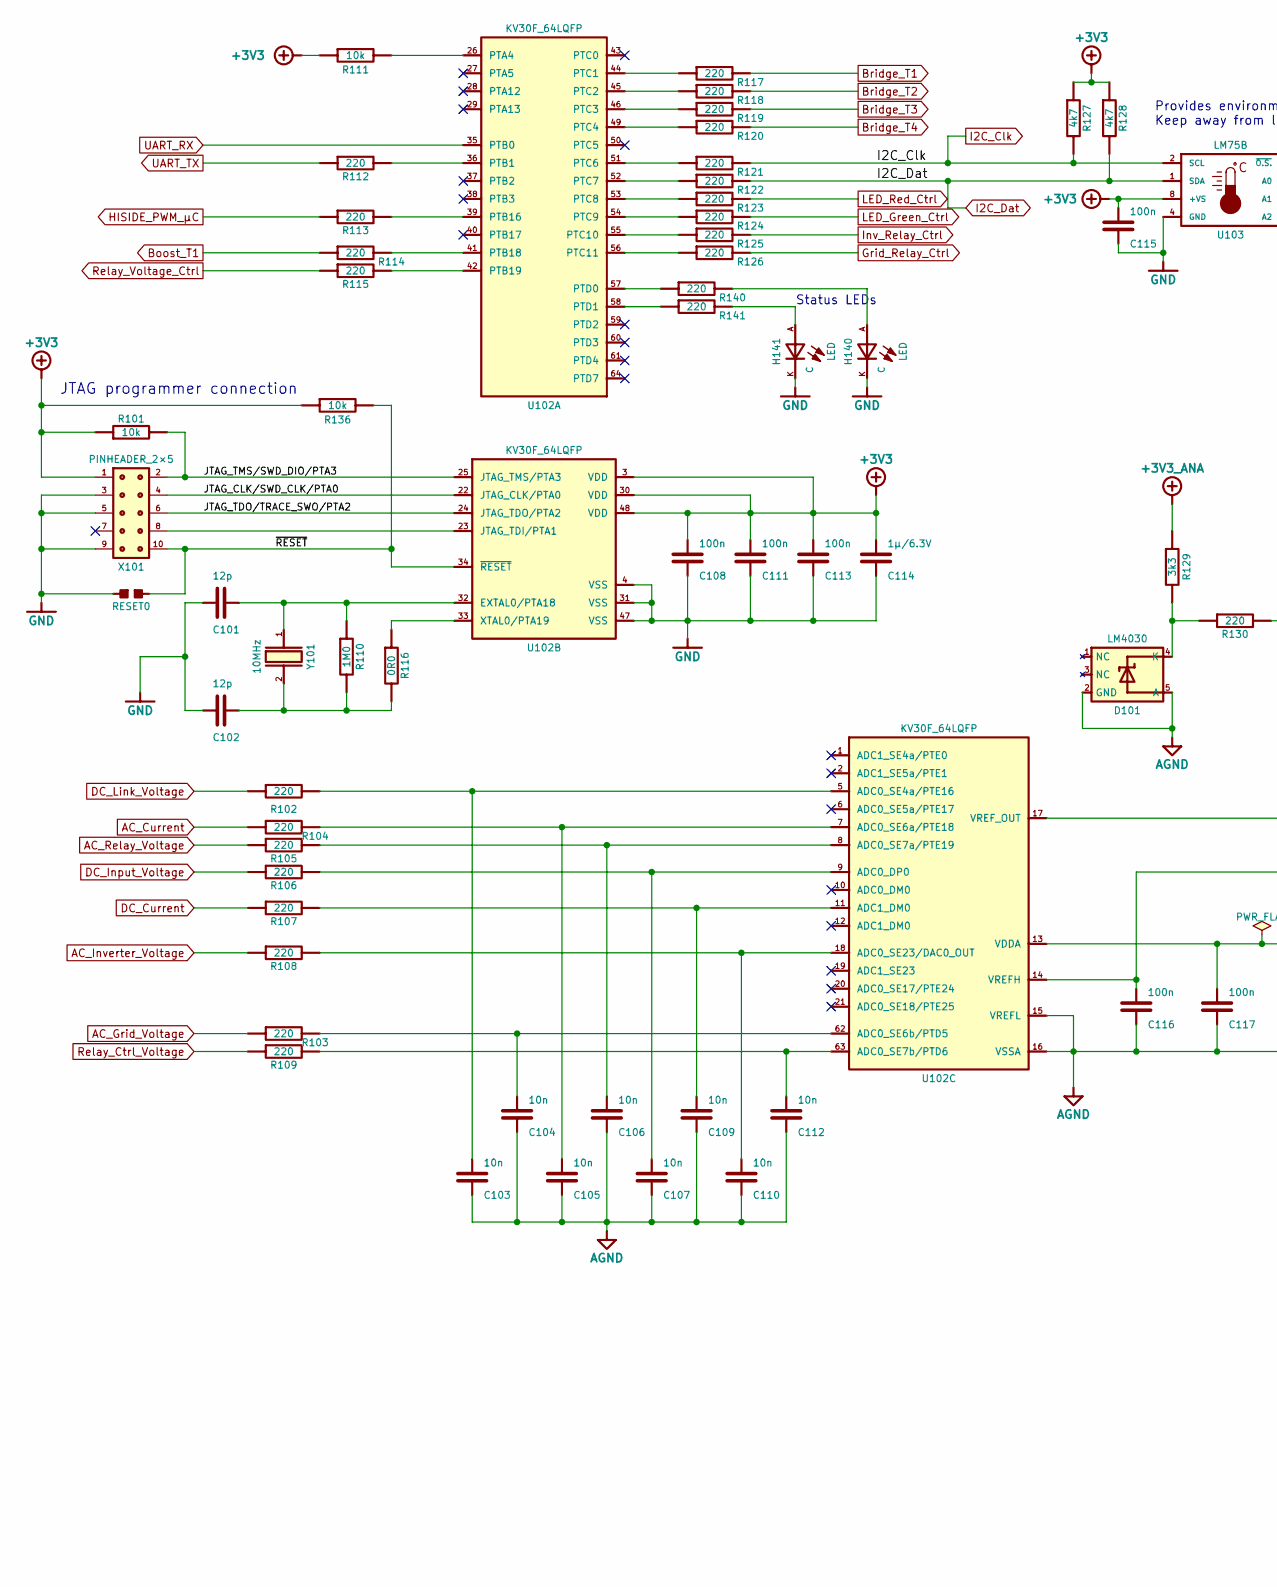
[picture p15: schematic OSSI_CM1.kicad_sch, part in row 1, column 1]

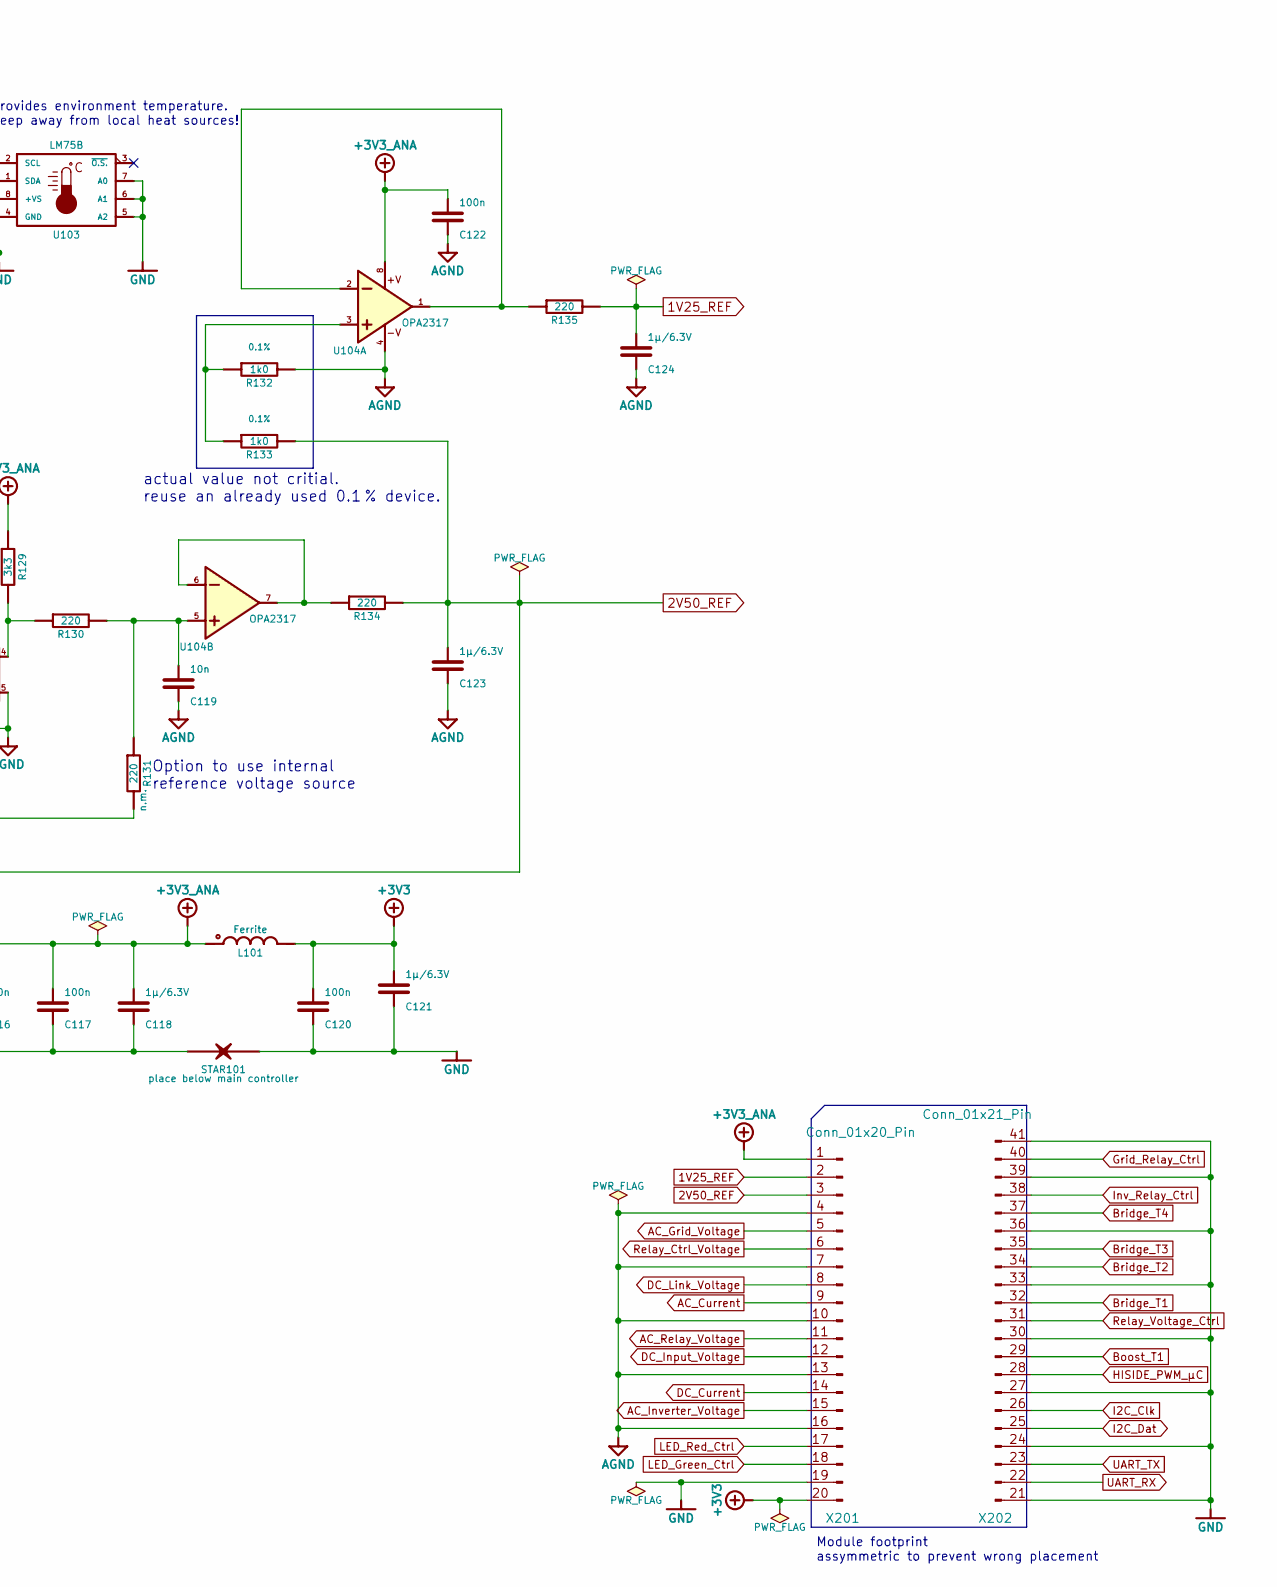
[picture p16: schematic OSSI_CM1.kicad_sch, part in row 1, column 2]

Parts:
C101, C102: 12p; 0603_W; Tolerance %; Partnumber P
C103, C104, C105, C106, C107, C109, C110, C112, C119: 10n; 0603_W; Tolerance %; Partnumber P
C108, C111, C113, C115, C116, C117, C120, C122: 100n; 0603_W; Tolerance %; Partnumber P
C114, C118, C121, C123, C124: 1µ/6.3V; 0805_W; Tolerance %; Partnumber P
D101: LM4030; SOT-23-5; Partnumber P
H140, H141: LED; 0603_W_LED; Partnumber P
L101: Ferrite; 0805_W; Partnumber P
R101, R111, R136: 10k; 0603_W; Tolerance %; Partnumber P
R102, R103, R104, R105, R106, R107, R108, R109, R112, R113, R114, R115, R117, R118, R119, R120, R121, R122, R123, R124, R125, R126, R130, R131, R134, R135, R140, R141: 220; 0603_W; Tolerance %; Partnumber P
R110: 1M0; 0603_W; Tolerance %; Partnumber P
R116: 0R0; 0603_W; Tolerance %; Partnumber P
R127, R128: 4k7; 0603_W; Tolerance %; Partnumber P
R129: 3k3; 0603_W; Tolerance %; Partnumber P
R132, R133: 1k0; 0603_W; Tolerance 0.1%; Partnumber P
RESET0: Solder_bridge_open; JUMPER_OPEN
STAR101: STARPOINT
U102: KV30F_64LQFP; LQFP-64_10x10_Pitch0.5mm; Partnumber P
U103: LM75B; SOIC8
U104: OPA2317; SOIC8; Partnumber P
X101: PINHEADER_2×5; PinHeader_2x05_P2.54mm_Vertical; Partnumber P
X201: Conn_01x20_Pin; PinHeader_1x20_P2.54mm_Vertical
X202: Conn_01x21_Pin; PinHeader_1x21_P2.54mm_Vertical
Y101: 10MHz; HC49_US; Partnumber P

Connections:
1V25_REF: C124.2, R135.2, X201.2
2V50_REF: C116.2, C123.2, R133.2, R134.2, U102.14 (VREFH), X201.3
+3V3: C108.2, C111.2, C113.2, C114.2, C115.2, C120.2, C121.2, L101.2, R101.1, R111.1, R127.1, R128.1, R136.1, U102.3 (VDD), U102.30 (VDD), U102.48 (VDD), U103.8 (+VS), X101.1, X201.20
+3V3_ANA: C117.2, C118.2, C122.2, L101.1, R129.1, U102.13 (VDDA), U104.8, X201.1
/JTAG_CLK/SWD_CLK/PTA0: U102.22 (JTAG_CLK/PTA0), X101.4
/JTAG_TDO/TRACE_SWO/PTA2: U102.24 (JTAG_TDO/PTA2), X101.6
/JTAG_TMS/SWD_DIO/PTA3: R101.2, U102.25 (JTAG_TMS/PTA3), X101.2
/~RESET: R136.2, RESET0.2, U102.34 (~RESET), X101.10
AC_Current: R104.1, X201.9
AC_Grid_Voltage: R103.1, X201.5
AC_Inverter_Voltage: R108.1, X201.15
AC_Relay_Voltage: R105.1, X201.11
AGND: C103.1, C104.1, C105.1, C106.1, C107.1, C109.1, C110.1, C112.1, C116.1, C117.1, C118.1, C119.1, C122.1, C123.1, C124.1, D101.2 (GND), D101.5 (A), R132.2, STAR101.1, U102.15 (VREFL), U102.16 (VSSA), U104.4, X201.4, X201.7, X201.10, X201.13, X201.16
Boost_T1: R114.1, X202.29
Bridge_T1: R117.2, X202.32
Bridge_T2: R118.2, X202.34
Bridge_T3: R119.2, X202.35
Bridge_T4: R120.2, X202.37
DC_Current: R107.1, X201.14
DC_Input_Voltage: R106.1, X201.12
DC_Link_Voltage: R102.1, X201.8
GND: C101.1, C102.1, C108.1, C111.1, C113.1, C114.1, C115.1, C120.1, C121.1, H140.K, H141.K, RESET0.1, STAR101.2, U102.4 (VSS), U102.31 (VSS), U102.47 (VSS), U103.4 (GND), U103.5 (A2), U103.6 (A1), U103.7 (A0), X101.3, X101.5, X101.9, X201.19, X202.21, X202.24, X202.27, X202.30, X202.33, X202.36, X202.39, X202.41
Grid_Relay_Ctrl: R126.2, X202.40
HISIDE_PWM_µC: R113.1, X202.28
I2C_Clk: R121.2, R127.2, U103.2 (SCL), X202.26
I2C_Dat: R122.2, R128.2, U103.1 (SDA), X202.25
Inv_Relay_Ctrl: R125.2, X202.38
LED_Green_Ctrl: R124.2, X201.18
LED_Red_Ctrl: R123.2, X201.17
unnamed: C102.2, R110.2, R116.2, Y101.2
unnamed: C109.2, R107.2, U102.11 (ADC1_DM0)
unnamed: C119.2, R130.2, R131.1, U104.5
unnamed: D101.4 (K), R129.2, R130.1
unnamed: H140.A, R140.2
unnamed: H141.A, R141.2
unnamed: R132.1, R133.1, U104.3
unnamed: R134.1, U104.6, U104.7
unnamed: R135.1, U104.1, U104.2
unnamed: R111.2, U102.26 (PTA4)
unnamed: R112.2, U102.36 (PTB1)
unnamed: R113.2, U102.39 (PTB16)
unnamed: R114.2, U102.41 (PTB18)
unnamed: R115.2, U102.42 (PTB19)
unnamed: R117.1, U102.44 (PTC1)
unnamed: R118.1, U102.45 (PTC2)
unnamed: R119.1, U102.46 (PTC3)
unnamed: R120.1, U102.49 (PTC4)
unnamed: R121.1, U102.51 (PTC6)
unnamed: R122.1, U102.52 (PTC7)
unnamed: R123.1, U102.53 (PTC8)
unnamed: R124.1, U102.54 (PTC9)
unnamed: R125.1, U102.55 (PTC10)
unnamed: R126.1, U102.56 (PTC11)
unnamed: R140.1, U102.57 (PTD0)
unnamed: R141.1, U102.58 (PTD1)
unnamed: C101.2, R110.1, U102.32 (EXTAL0/PTA18), Y101.1
unnamed: U102.23 (JTAG_TDI/PTA1), X101.8
unnamed: R116.1, U102.33 (XTAL0/PTA19)
unnamed: C107.2, R106.2, U102.9 (ADC0_DP0)
unnamed: C103.2, R102.2, U102.5 (ADC0_SE4a/PTE16)
unnamed: C105.2, R104.2, U102.7 (ADC0_SE6a/PTE18)
unnamed: C104.2, R103.2, U102.62 (ADC0_SE6b/PTD5)
unnamed: C106.2, R105.2, U102.8 (ADC0_SE7a/PTE19)
unnamed: C112.2, R109.2, U102.63 (ADC0_SE7b/PTD6)
unnamed: C110.2, R108.2, U102.18 (ADC0_SE23/DAC0_OUT)
unnamed: R131.2, U102.17 (VREF_OUT)
Relay_Ctrl_Voltage: R109.1, X201.6
Relay_Voltage_Ctrl: R115.1, X202.31
UART_RX: U102.35 (PTB0), X202.22
UART_TX: R112.1, X202.23

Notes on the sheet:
JTAG programmer connection
Provides environment temperature. Keep away from local heat sources!
Option to use internal reference voltage source
Module footprint assymmetric to prevent wrong placement
Status LEDs
actual value not critial. reuse an already used 0.1 % device.

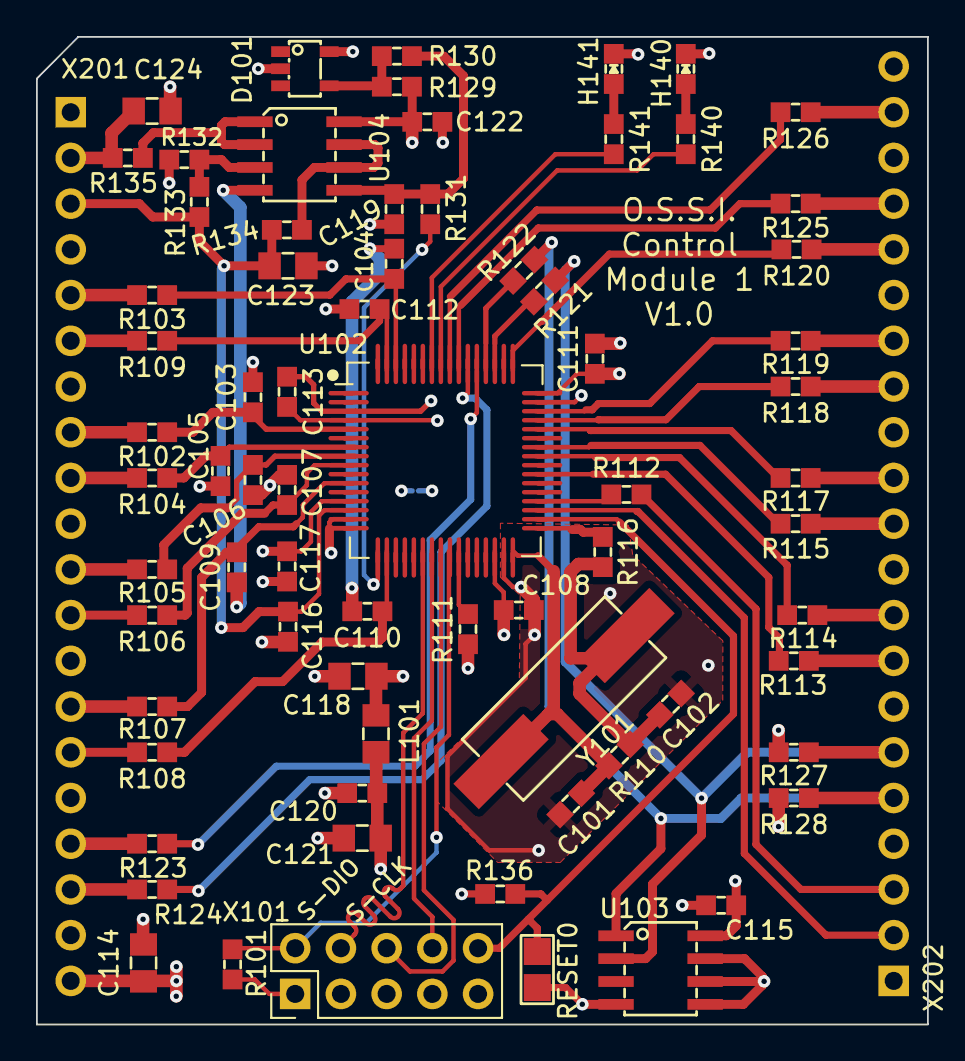
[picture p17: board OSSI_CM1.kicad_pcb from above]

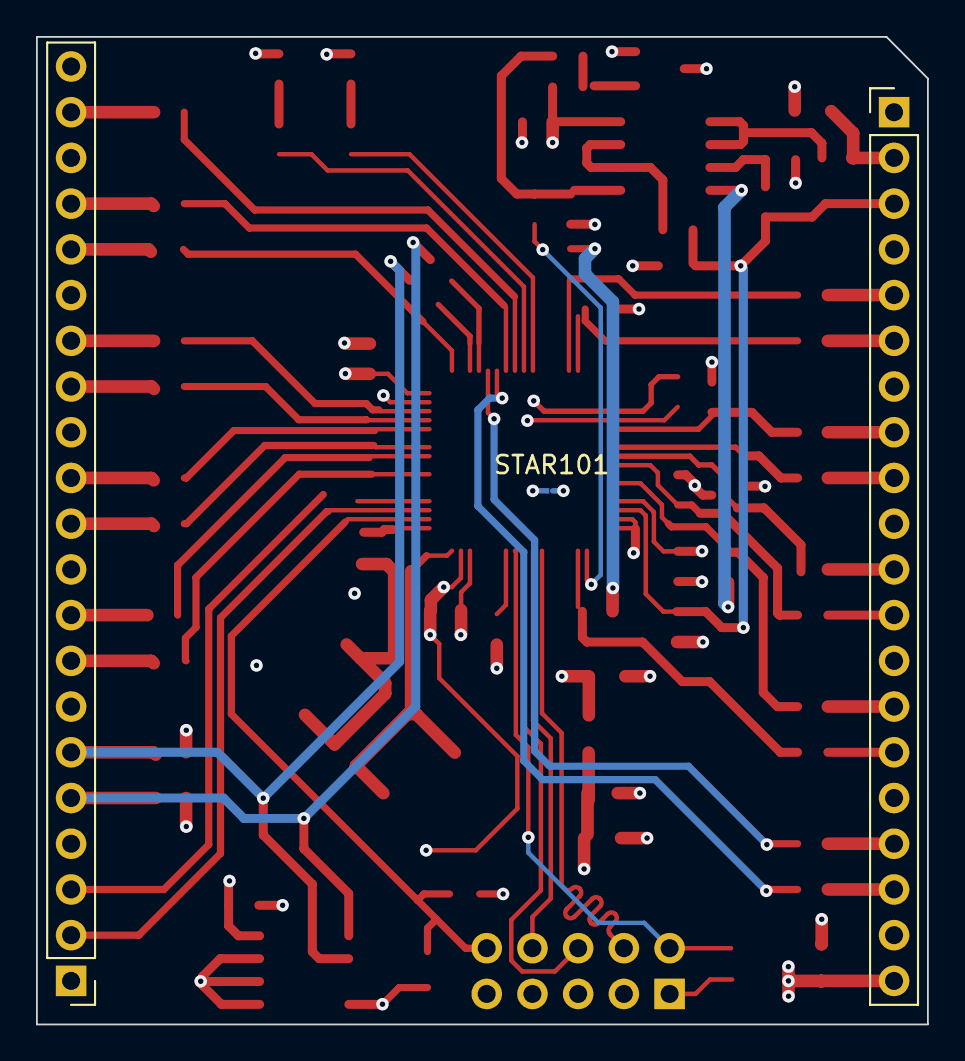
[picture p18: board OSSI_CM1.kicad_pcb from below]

Board: 4 copper layers, 49.5 x 54.9 mm, 75 parts (3 on the bottom side), 70 nets.

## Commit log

2016-03-06 Add project standard library, Init project schematic
    [AC_filter.sch, AC_switch.sch, Analog_frontend.sch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]
2016-03-10 Add analog frontend, add needed libraries
    [AC_filter.sch, AC_switch.sch, DC_booster.sch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]
2016-03-22 Add more circuitry, add library content
    AC current measurement
    AC filter
    AC switch
    DC booster
    DC input
    Analog frontend
    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
    [AC_current_measurement.sch, AC_filter.sch, AC_switch.sch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]
2017-03-26 Updates all schematic pages to current components
    all components are replaced with the current component library parts
    [AC_current_measurement.sch, AC_filter.sch, AC_switch.sch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]
2018-04-15 fixes power symbols and pin attributes in library,
    adds various footprints
    [analog_frontend.sch]
2018-08-09 adds footprints and new component libs
2019-08-31 bulk-updates libraries and schematics
    schematic is updated to Kicad 5.1.14
    updates various sheets with new circuits
    adds various component libraries
    [AC_current_measurement.sch, AC_filter.sch, AC_switch.sch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]
2019-12-12 updates schematics, adds high side power supply
    for inverter bridge
    adds required components to library and footprints
    [highside_supply.sch]
2021-05-25 minor updates and cleaup
    [AC_current_measurement.sch, AC_filter.sch, AC_switch.sch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]
2021-05-25 adds footprints
2022-10-05 converts project to Kicad V6 file formats
    [AC_current_measurement.kicad_sch, AC_filter.kicad_sch, AC_switch.kicad_sch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]
2022-10-10 converts libraries to Kicad 6 format, updates bridge driver
    [AC_current_measurement.kicad_sch, AC_switch.kicad_sch, DC_booster.kicad_sch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]
2022-10-15 updates circuits, adds linear regulator NCP1117
    [OSSI_MK_I.kicad_sch, analog_frontend.kicad_sch, drivers.kicad_sch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]
2022-10-16 adds interface schematic and NodeMCU symbol for it
    [OSSI_MK_I.kicad_sch, interface.kicad_sch, main_controller.kicad_sch]
2022-10-30 adds pin headers for display options
    [OSSI_MK_I.kicad_sch, interface.kicad_sch, main_controller.kicad_sch]
2023-05-10 converts the project to Kicad 7
    [AC_current_measurement.kicad_sch, AC_filter.kicad_sch, AC_switch.kicad_sch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]
2023-11-25 adds the Control Module to the circuits
    [OSSI_CM1.kicad_pcb, OSSI_CM1.kicad_sch]
2023-11-25 replaces controller schematics with Control Module 1
    [OSSI_MK_I.kicad_sch]
2023-12-04 adds compute module 2 (CM2) based on STM32-L412
    [OSSI_CM2.kicad_pcb, OSSI_CM2.kicad_sch]
2024-01-04 Updates footprint paths
    [OSSI_CM1.kicad_pcb, OSSI_CM1.kicad_sch, OSSI_CM2.kicad_pcb]
2024-01-21 adds fabrication files and HTML bom for easier access
    [OSSI_CM1-B_Cu.gbr, OSSI_CM1-B_Mask.gbr, OSSI_CM1-B_Paste.gbr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]
2024-01-29 updates PCB with pinout comments, adds pinout PDF
    [OSSI_CM2.kicad_pcb]
2024-01-30 adds pin description for debug port
    [OSSI_CM2.kicad_pcb]
2024-02-03 adds version V1.1 of CM2 containing fixes vs V1.0
    [OSSI_CM2.kicad_pcb, OSSI_CM2.kicad_sch]
2024-02-03 improves symbol desing to prevent confusion when reading schematics
2024-02-03 adds a binary for initial operation tests
    blinks the two on-board LEDs, reads inputs for ADC1, reads temperature sensor, outputs 2 PWMs, outputs some text via UART (115200 bds).
2024-02-10 adds remark for resistor tolerances
2024-02-10 updates CM2 symbol, updates CM1 symbol, adds footprint for Control Modules
    [AC_current_measurement.kicad_sch, OSSI_MK_I.kicad_sch, drivers.kicad_sch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]
2024-02-10 exchanges control module to CM2 as default control module
    [OSSI_MK_I.kicad_sch]
2024-02-10 minor fixes to routing to several resistor pads
    [OSSI_CM2.kicad_pcb]
2024-03-04 adds control module 2.0 and required library files
    [OSSI_CM2.kicad_pcb, OSSI_CM2.kicad_sch]
2024-03-05 cleans up routing, library links, library 3D models
    [OSSI_CM2.kicad_pcb, OSSI_CM2.kicad_sch]
2024-03-06 cleans up schematic, rearranges some signals and components for better readability
    [OSSI_CM2.kicad_sch]
2024-03-10 cleans up and rearranges schematics for more clarity
    [OSSI_CM2.kicad_pcb, OSSI_CM2.kicad_sch]
